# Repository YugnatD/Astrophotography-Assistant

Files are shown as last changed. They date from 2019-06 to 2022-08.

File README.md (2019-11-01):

# Astrophotography-Assistant

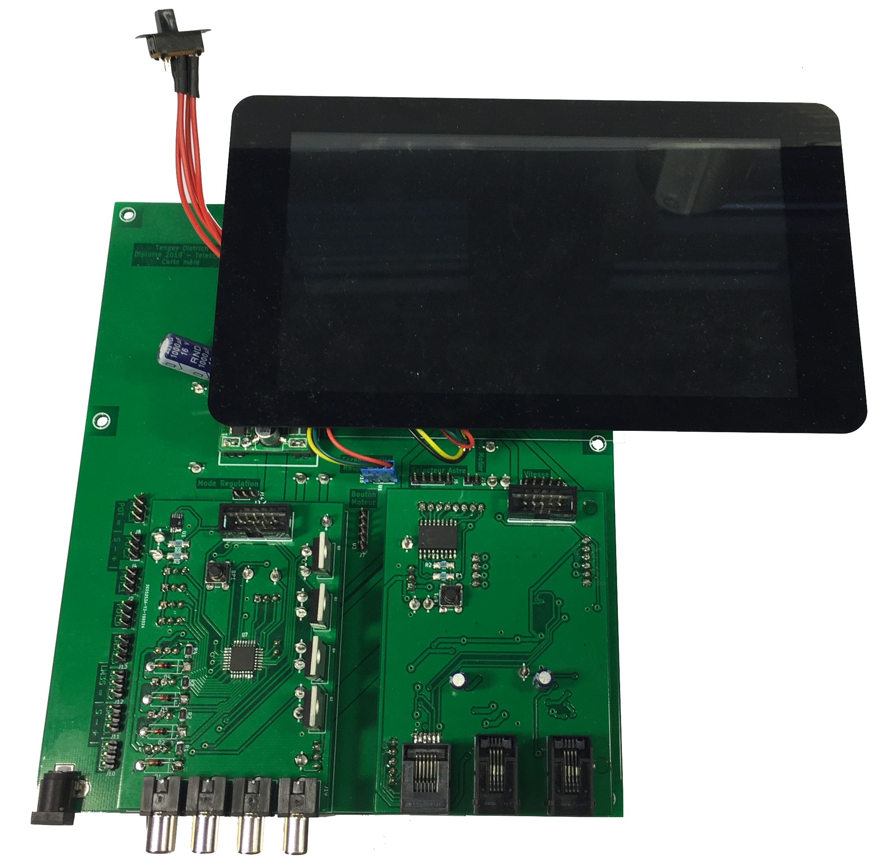
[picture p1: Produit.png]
Astrophotography-Assistant


The project has two utility :
Make an automatic regulation of the temperature of the mirror of a newtonian telescope.
Recreate a card to controle motor of a NEQ5 mount, to add more correction speed, and planetary speed.

There is a raspberry pi integrated to the card that can control a guiding camera using PHD2.

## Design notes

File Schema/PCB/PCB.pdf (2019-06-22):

9.5.Dossier de fabrication des circuits imprimés

Projet / produit : | Diplôme 2019 - Télescope

Description :

Quantités : | 1 pièce _ pièces / lot de fabrication _ pièces / an

Circuit :

Nom : | Carte Mere
Numéro : | ND (non disponible)
Révision : | 3
Date de création : | 28.05.2019 | Auteur : | Tanguy Dietrich

Historique des modifications :

Rév. | Date | Auteur | Détails des modifications
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
Spécification du PCB :

Nature du matériel isolant : | Bakélite | FR-2 | ___
Epoxy | FR-4 | ___
Autre : ___
Epaisseur du PCB : | 0.5 mm | 0.8 mm | | 1.0 mm | 1.2 mm
| 1.6 mm | 2.0 mm | | autre : _ mm
Nombre de couches : | Simple face
Double face
Multicouches, nombre de couches = X

Epaisseur des couches cuivre :
Externe | 18 P | 35 P | 75 P | 105 P | autre :
_
Interne | 18 P | 35 P | 75 P | 105 P | autre :
_
Largeur minimum des pistes : | 0.508 | mm / | 20m | inch
Largeur minimum entre pistes : | 0.254 | mm / | 10m | inch

Liste des documents :

Liste du matériel | Page 3
Dimensions du PCB | Page 4
Plan de perçage | Page 5
Plan | d’implantation
dessous
| Page 6
Plan | d’implantation
dessus
| Page 6
Print : vue de dessous | Page 7
Print : vue de dessus | Page 7
Points tests | Page 8
Fichier Gerber | ___

Liste du matériel :

Références | Composant | N° article Distrelec | Quantité | Pu [CHF] | Ptot [CHF]
C1 | 100uF 16V radial 5mm | 300-92-017 | 1 | 0.063 | 0.063
J1 | Connecteur jack-DC | 301-29-715 | 1 | 0.4335 | 0.4335
J2; J4; J8; J9; J10; J11; J12; J13; J14 | Connecteur 3 pin Male | 300-93-644 | 9 | 0.1317 | 1.1853
J3 | Connecteur 2*20 Femelle (raspberry Pi) | 300-93-679 | 1 | 2.05 | 2.05
J5; J6; J7 | Connecteur 5 pins Male | 300-93-646 | 3 | 0.2346 | 0.7038
J15 | Connecteur 2 pins Male | 300-93-652 | 1 | 0.176 | 0.176
J16; J17; J19; J20; J21; J22; J23; J24; J25 | Cosse poignard | | 9
J18 | Connecteur 4 pins Male | 300-93-645 | 1 | 0.1761 | 0.1671
JP1 | Connecteur 3 Pin male modifier | 300-93-644 | 2 | 0.1317 | 0.2634
R1; R2; R3; R4; R5; R6; R7; R8; R9; R10; R11; R12; R13 | Résistance SMD 1206 10 [kOhm] | 300-56-987 | 13 | 0.0285 | 0.3705
U1 | Carte moteur | | 1 | 18.1567 | 18.1567
J3 | Raspberry Pi 3 B+ | 301-09-158 | 1 | 39.6 | 39.6
J3 | LCD 7 pouces pour Raspberry Pi | 300-37-316 | 1 | 86.90 | 86.90
U2 | Carte LM2576 | | 1 | 4.6161 | 4.6161
U3 | Carte Température | | 1 | 55.44 | 55.44
U3,U2 | Connecteur 2 pins femelles | 300-93-662 | 5 | 0.5385 | 2.6925
U3,U1 | Connecteur 3 pins femelles | 300-93-663 | 11 | 0.8973 | 9.8703
U1 | Connecteur 4 pins femelles | 300-93-664 | 1 | 0.8973 | 0.8973
U1 | Connecteur 5 pins femelles | 300-93-665 | 1 | 0.9972 | 0.9972
U1 | Connecteur 6 pins femelles | 300-93-666 | 1 | 0.9971 | 0.9971
U1 | Connecteur 8 pins femelles | 300-93-668 | 1 | 1.14 | 1.14
PCB carte Mere | | | 1 | 2.98 | 2.98
Prix total = | | | | 229.6998 [CHF]

Dimensions de la carte :

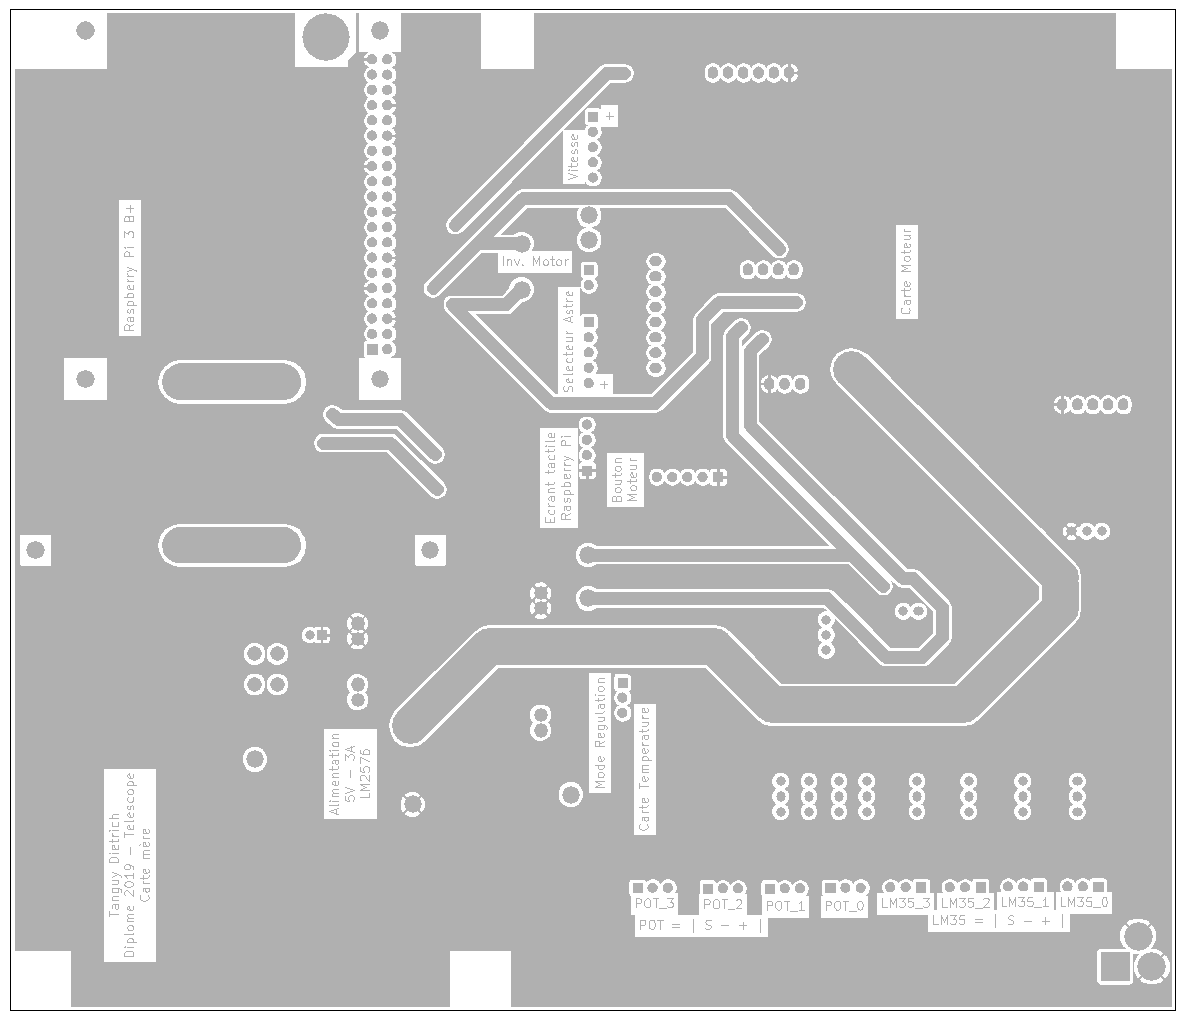
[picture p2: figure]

194mm x 166.7mm

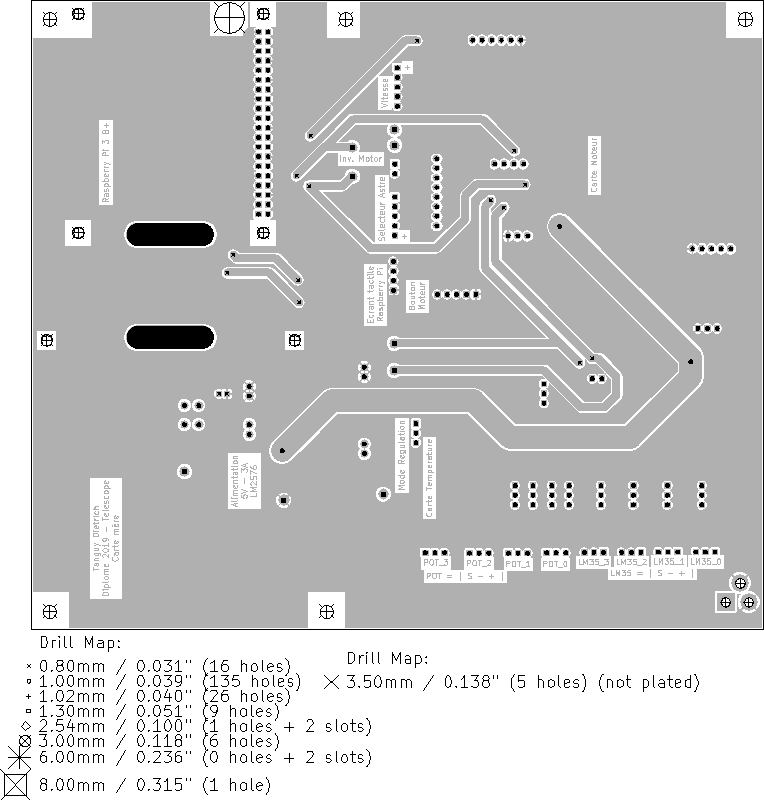
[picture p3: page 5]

Plan de perçage :

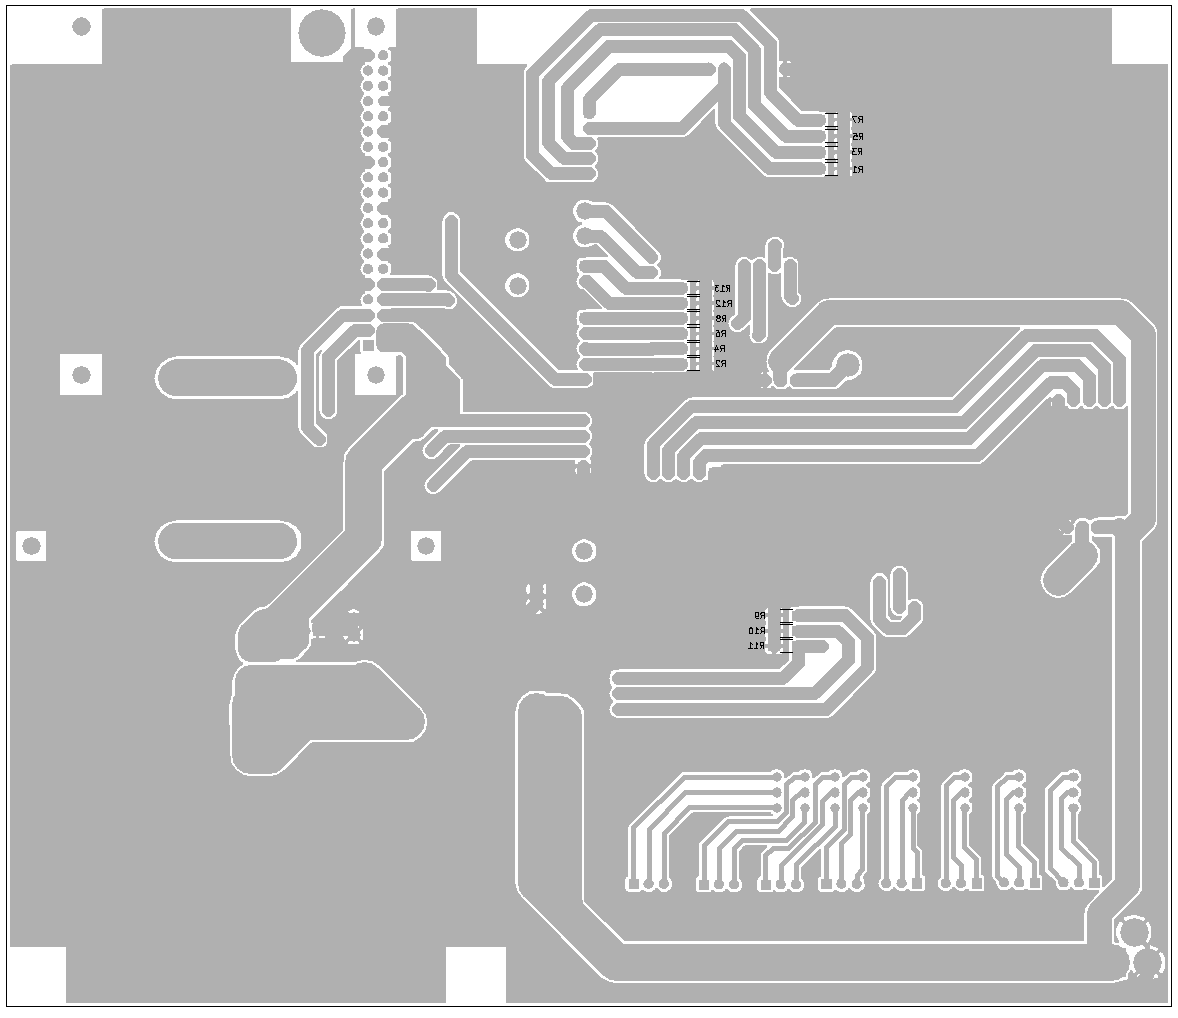
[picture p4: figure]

Plan d’implantation dessous :

Plan d’implantation dessus :

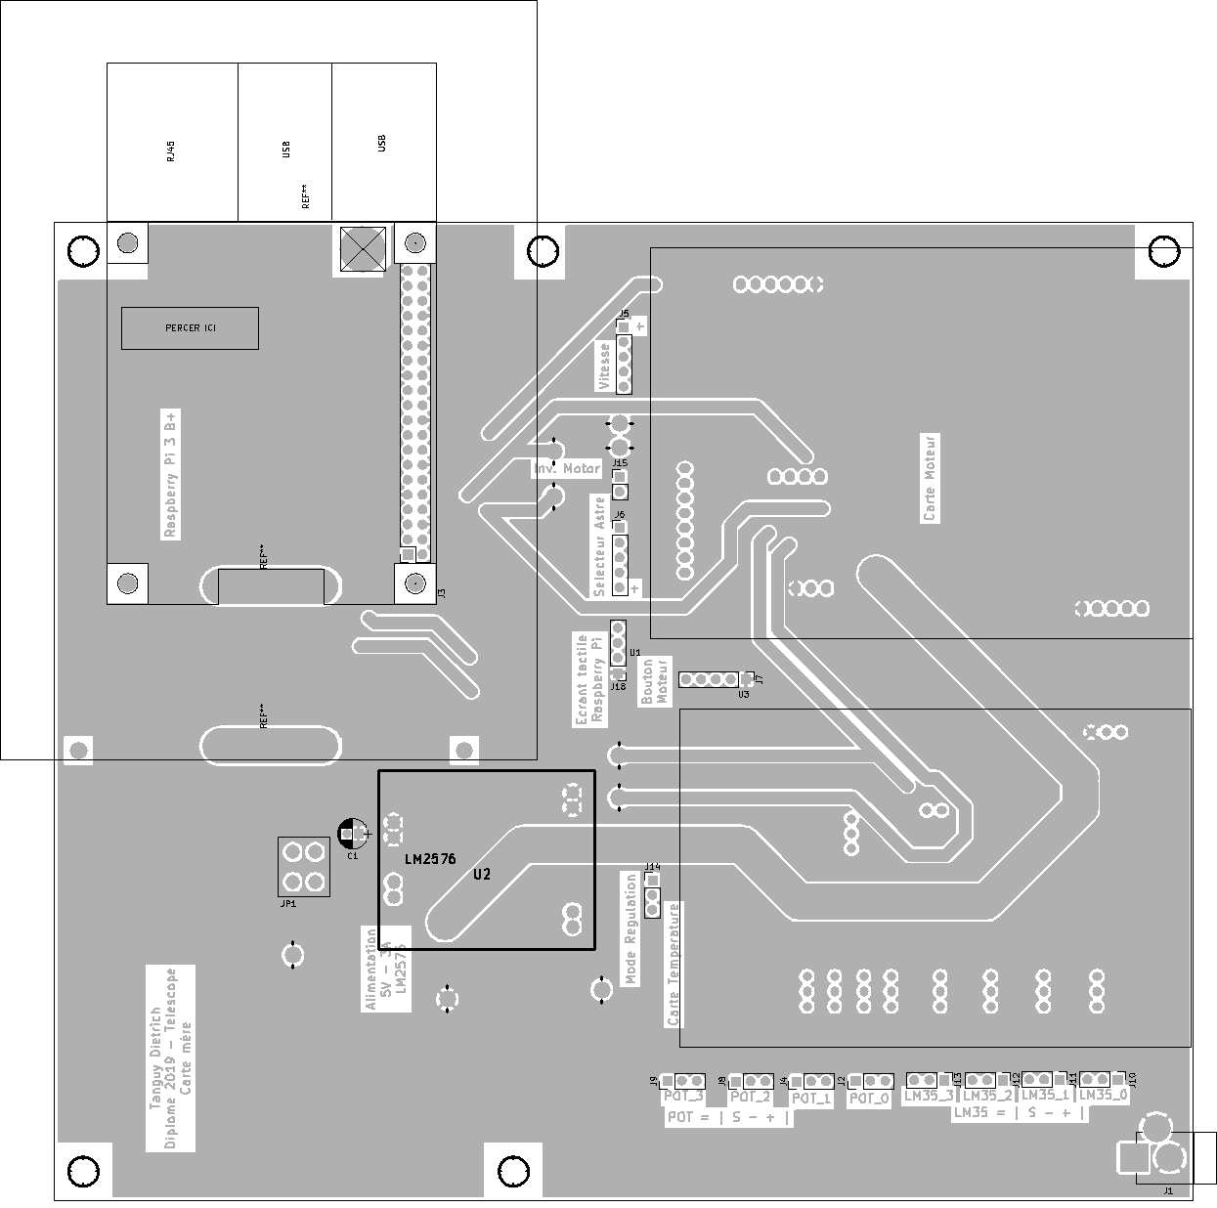
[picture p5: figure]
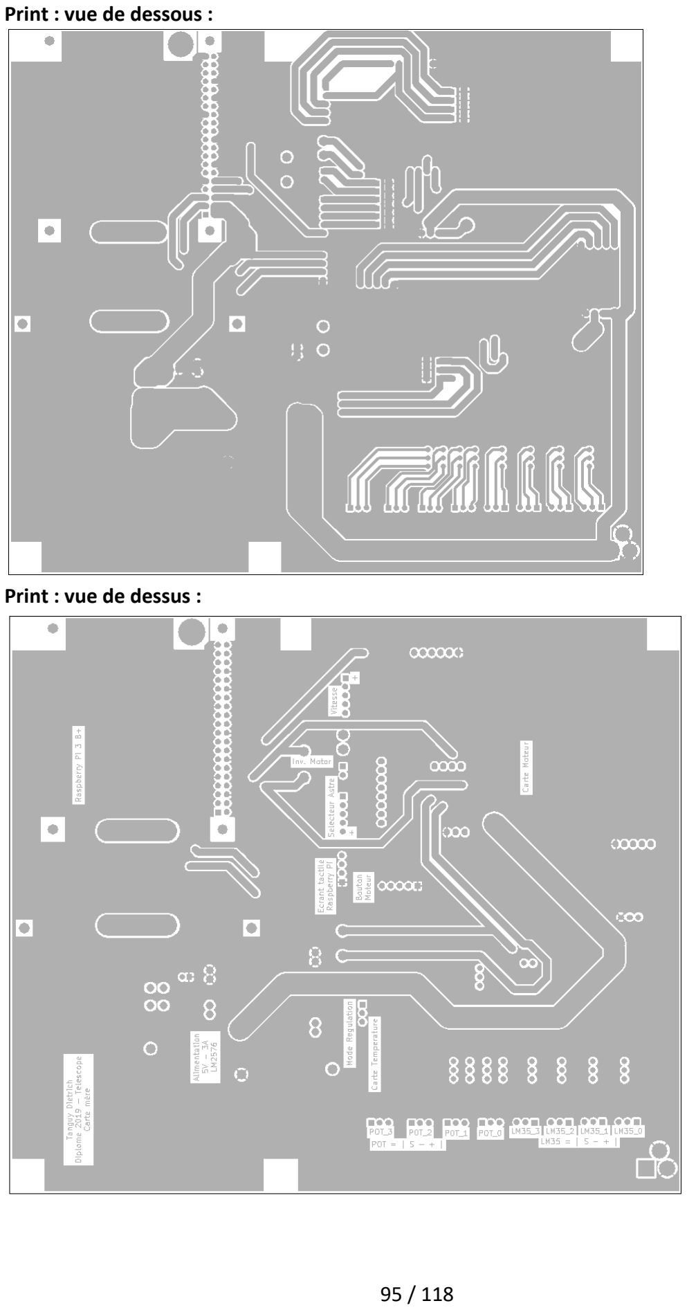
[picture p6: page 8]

Print : vue de dessous :

Print : vue de dessus :

Points tests :

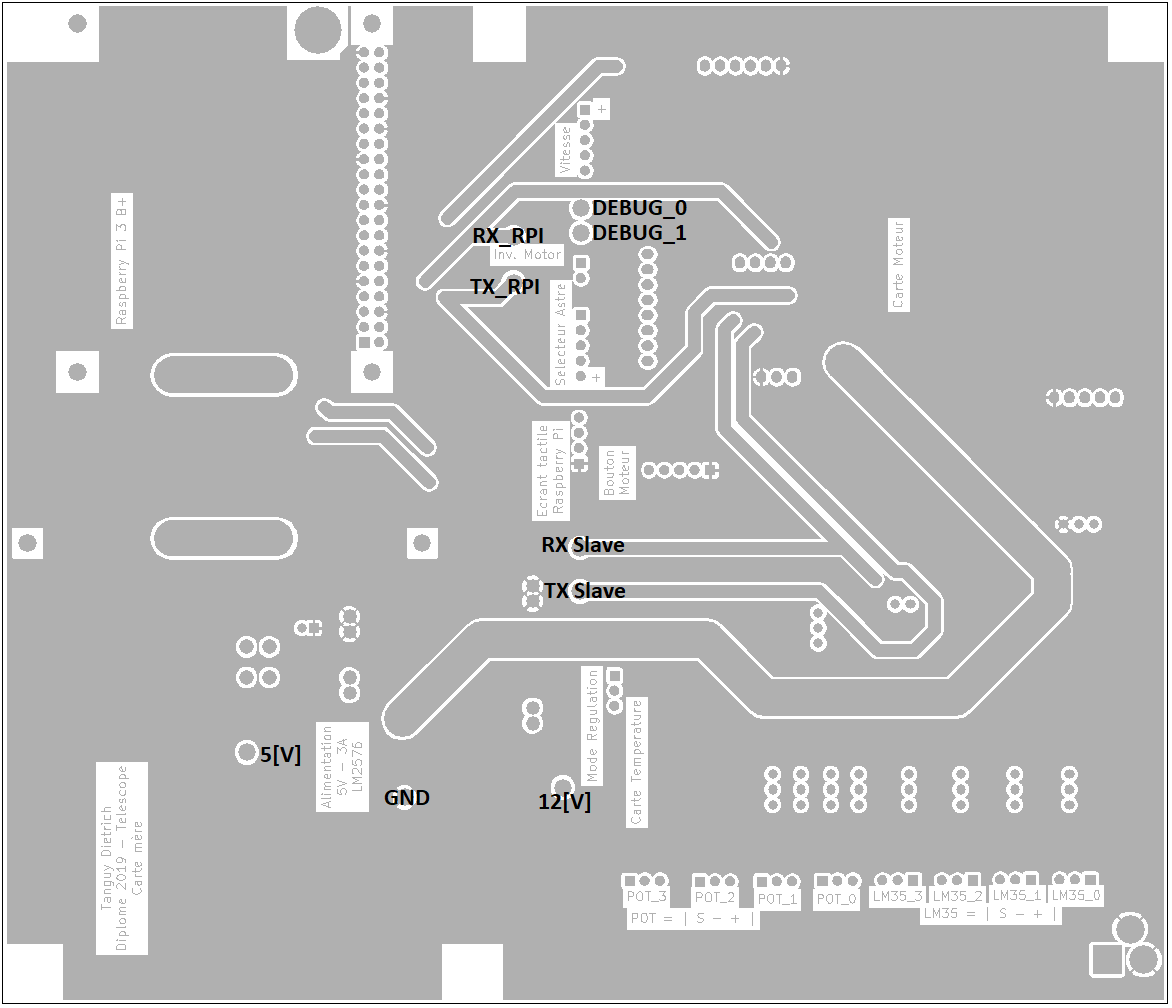
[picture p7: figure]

Projet / produit : | Diplôme 2019 - Télescope

Description :

Quantités : | 1 pièce _ pièces / lot de fabrication _ pièces / an

Circuit :

Nom : | Carte de gestion de la température
Numéro : | ND (Non disponible)
Révision : | 0
Date de création : | 17.09.2018 | Auteur : | Tanguy Dietrich

Historique des modifications :

Rév. | Date | Auteur | Détails des modifications
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
Spécification du PCB :

Nature du matériel isolant : | Bakélite | FR-2 | ___
Epoxy | FR-4 | ___
Autre : ___
Epaisseur du PCB : | 0.5 mm | 0.8 mm | | 1.0 mm | 1.2 mm
| 1.6 mm | 2.0 mm | | autre : _ mm
Nombre de couches : | Simple face
Double face
Multicouches, nombre de couches = X

Epaisseur des couches cuivre :
Externe | 18 P | 35 P | 75 P | 105 P | autre :
_
Interne | 18 P | 35 P | 75 P | 105 P | autre :
_
Largeur minimum des pistes : | 0.508 | mm / | 20m | inch
Largeur minimum entre pistes : | 0.254 | mm / | 10m | inch

Liste des documents :

Liste du matériel | Page 3
Dimensions du PCB | Page 4
Plan de perçage | Page 5
Plan | d’implantation
dessous
| Page 6
Plan | d’implantation
dessus
| Page 6
Print : vue de dessous | Page 7
Print : vue de dessus | Page 7
Points tests | Page 8
Fichier Gerber | ___

Liste du matériel :

Références | Composant | Référence fabricant | Quantité | Pu [CHF] | Ptot [CHF]
BP1 | Bouton Poussoir | 301-18-595 | 1 | 0.2111 | 0.2111
C1 | 100nF SMD 1206 | 300-67-988 | 1 | 0.1094 | 0.1094
C11 | 1uF SMD 1206 | 300-86-875 | 1 | 0.0496 | 0.0496
D1,D2,D3,D4 | 1N4148 | 300-92-887 | 4 | 0.0175 | 0.07
J1; J2; J3; J4; J5; J6; J7; J8; J9; J13 | Connecteur 3 pins male | 300-93-644 | 10 | 0.1317 | 1.317
J12 | Connecteur 10 pins | 300-12-021 | 1 | 0.87 | 0.87
J18; J19; J24; J25 | Connecteur RCJ | 490-RCJ-041 | 4 | 1.36 | 5.44
Q1; Q2; Q3; Q4 | IRL3705 TO-220 | 171-18-037 | 4 | 1.91 | 7.64
R1; R2; R3; R4, | Résistance 18k 1206 | 300-56-931 | 4 | 0.0344 | 0.1376
R5; R6 ;R15 ;R16 ;R17 | Résistance 1k 1206 | 300-56-986 | 5 | 0.0285 | 0.1425
U1 | EEH210 | 300-73-044 | 1 | 10.30 | 10.30
U7 | C8051F38C | | 1 | 1.44 | 1.44
PCB | PCB carte température | | 1 | 1 | 1
LM35 | LM35 capteur température | 173-26-716 | 4 | 3.2 | 12.8
potentiomètre | | 164-35-367 | 4 | 3.65 | 14.6
Prix total = | | | | 55.4432 [CHF]

Dimensions de la carte :

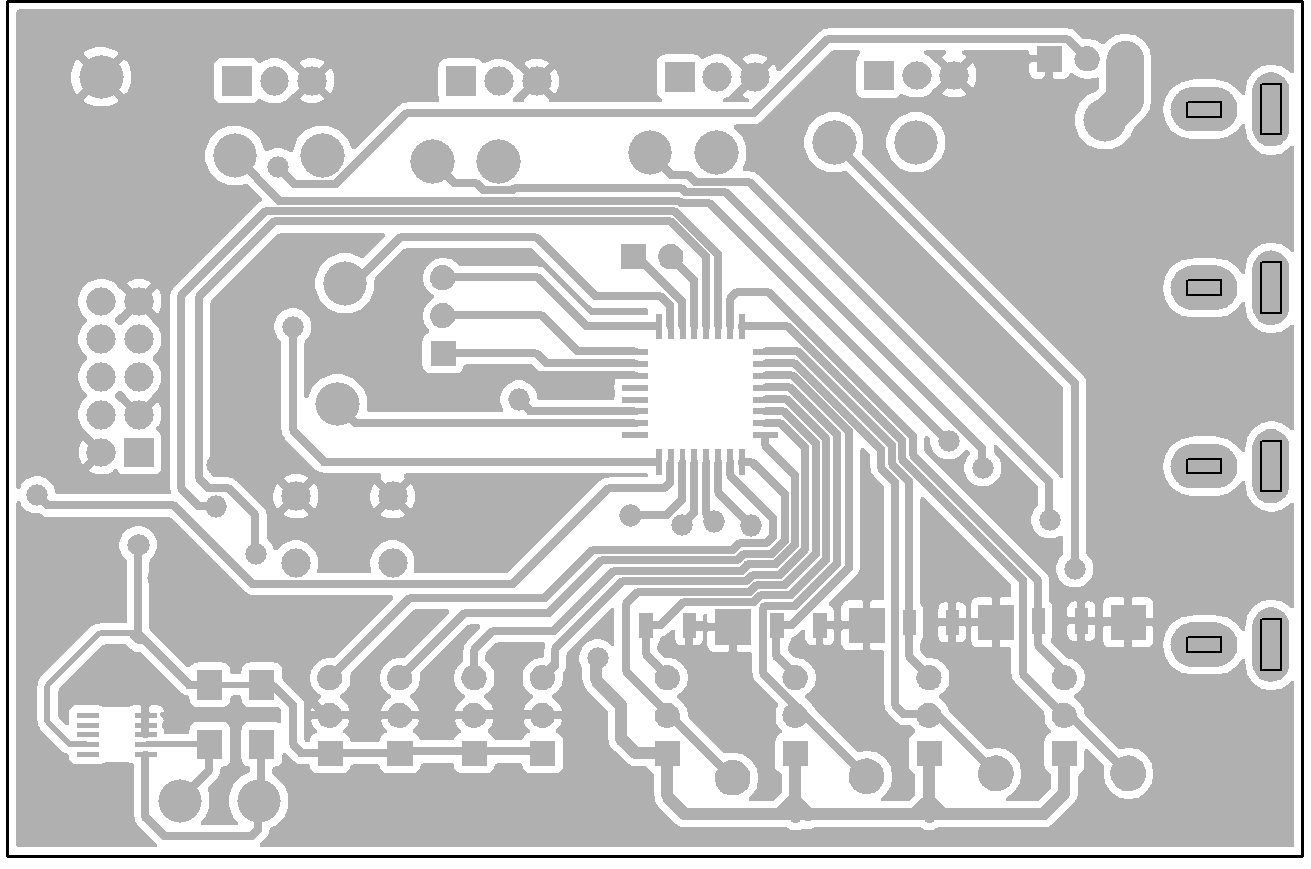
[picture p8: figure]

La carte fait 87.1mm x 57.5 mm

Plan de perçage :

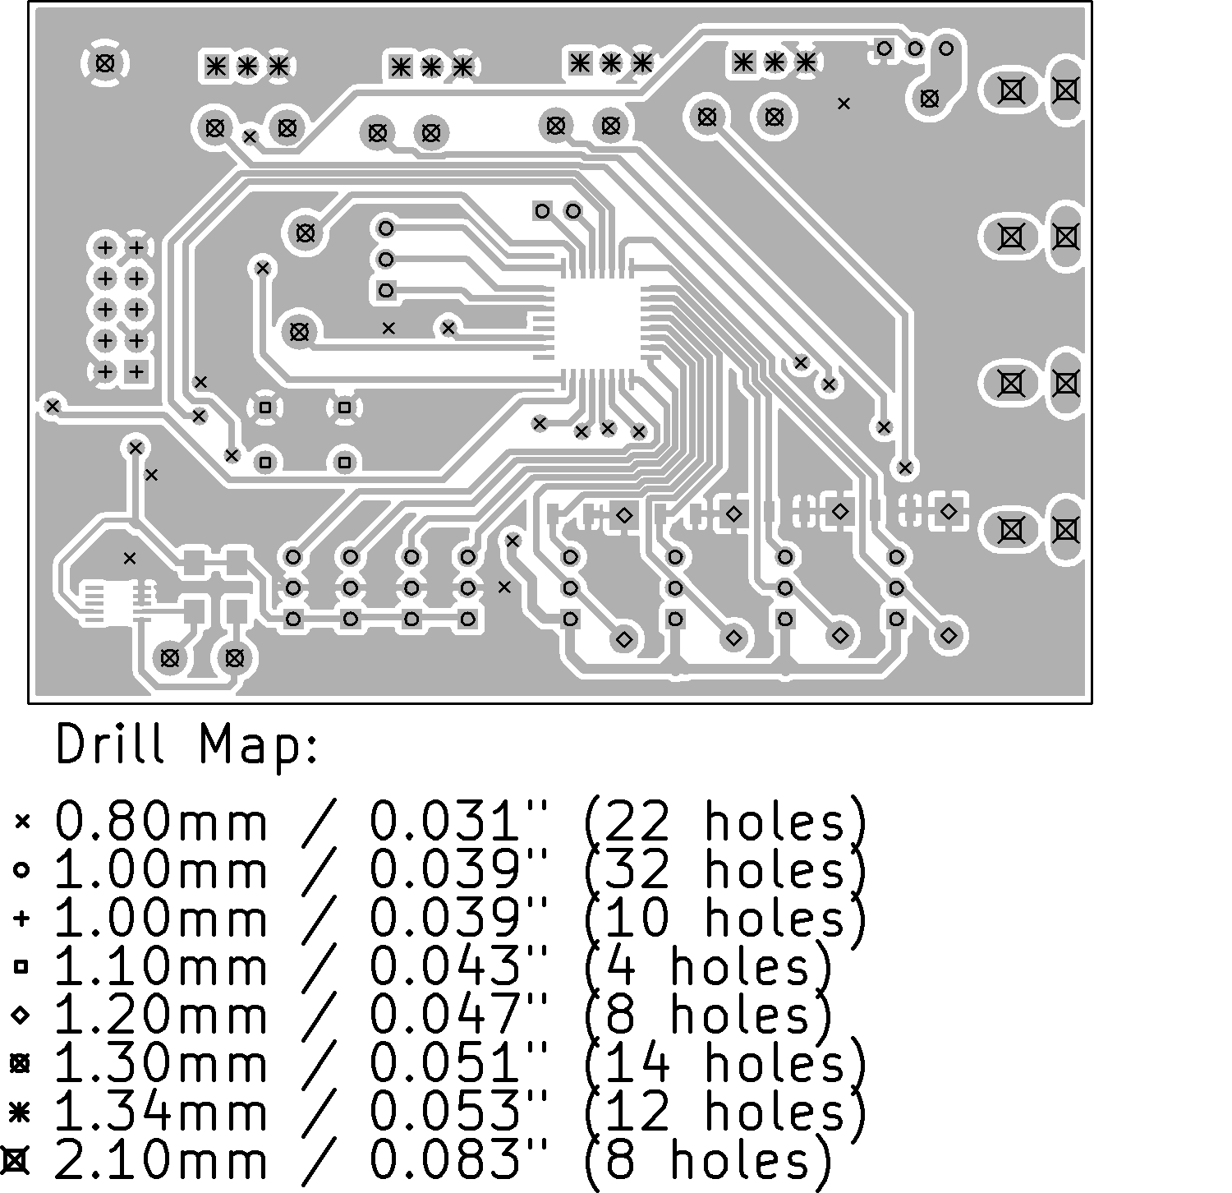
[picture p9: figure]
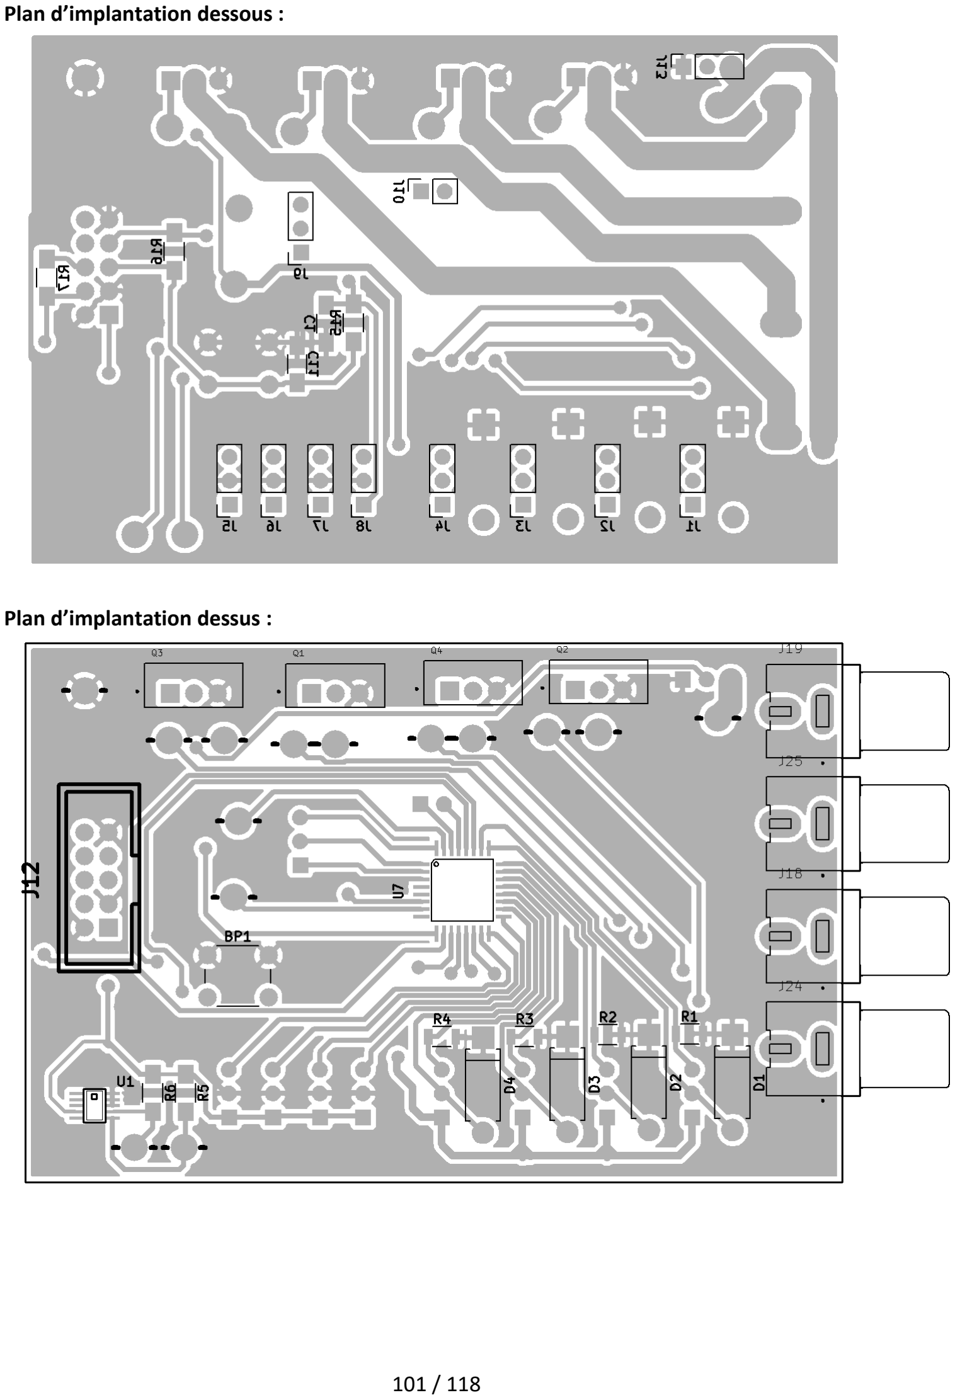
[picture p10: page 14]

Plan d’implantation dessous :

Plan d’implantation dessus :

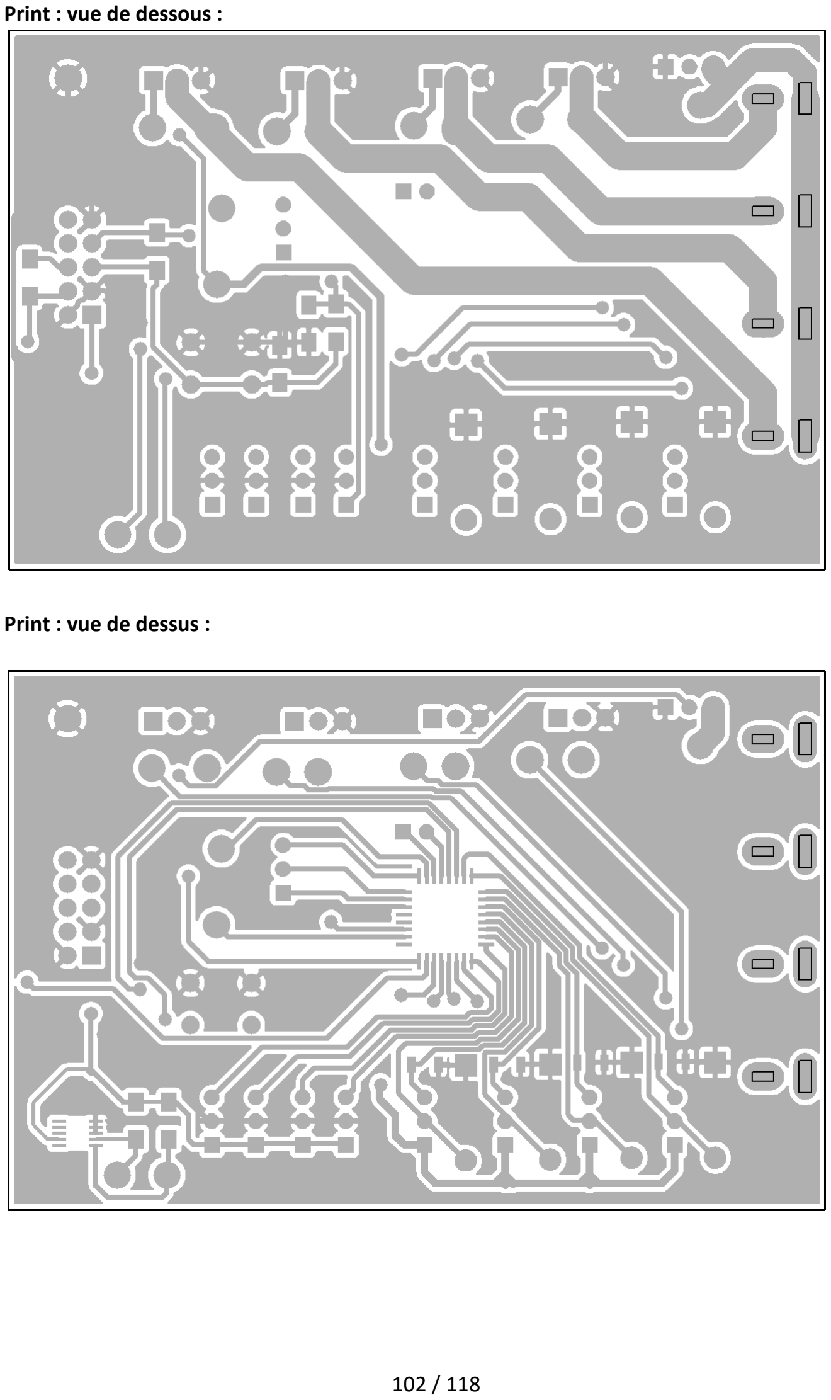
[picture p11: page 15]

Print : vue de dessous :

Print : vue de dessus :

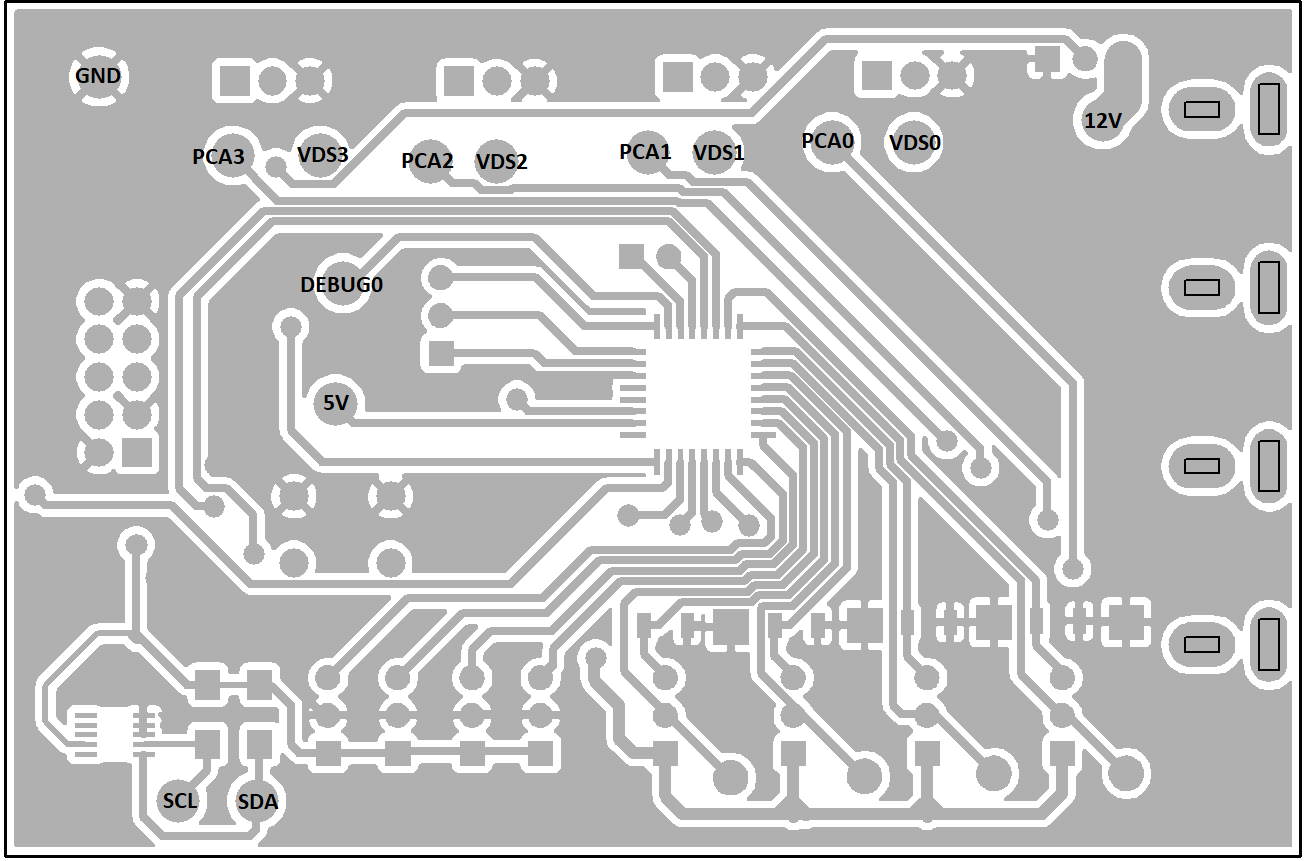
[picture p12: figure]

Points tests :

Projet / produit : | Diplôme 2019 - Télescope

Description :

Quantités : | 1 pièce _ pièces / lot de fabrication _ pièces / an

Circuit :

Nom : | Alimentation 5V – 3A
Numéro : | ND (non disponible)
Révision : | 0
Date de création : | 17.09.2018 | Auteur : | Tanguy Dietrich

Historique des modifications :

Rév. | Date | Auteur | Détails des modifications
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
Spécification du PCB :

Nature du matériel isolant : | Bakélite | FR-2 | ___
Epoxy | FR-4 | ___
Autre : ___
Epaisseur du PCB : | 0.5 mm | 0.8 mm | | 1.0 mm | 1.2 mm
| 1.6 mm | 2.0 mm | | autre : _ mm
Nombre de couches : | Simple face
Double face
Multicouches, nombre de couches = X

Epaisseur des couches cuivre :
Externe | 18 P | 35 P | 75 P | 105 P | autre :
_
Interne | 18 P | 35 P | 75 P | 105 P | autre :
_
Largeur minimum des pistes : | 0.508 | mm / | 20m | inch
Largeur minimum entre pistes : | 0.254 | mm / | 10m | inch

Liste des documents :

Schéma électrique | Page 3
Liste du matériel | Page 3
Dimensions du PCB | Page 4
Plan de perçage | Page 5
Plan | d’implantation
dessous
| Page 6
Plan | d’implantation
dessus
| Page 6
Print : vue de dessous | Page 7
Print : vue de dessus | Page 7
Points tests | Page 8
Fichier Gerber | ___

Schéma électrique :

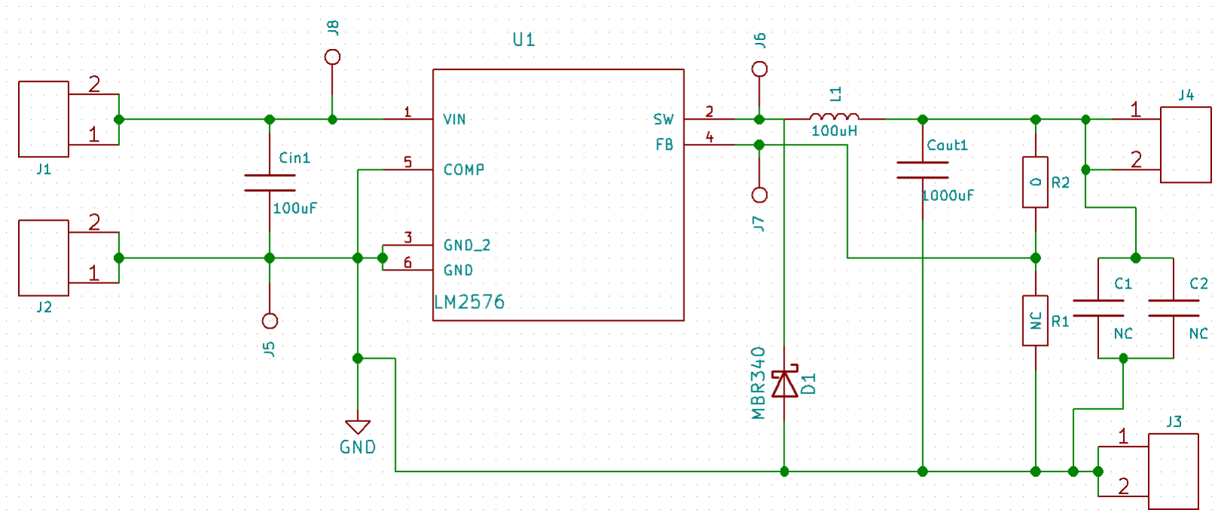
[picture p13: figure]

Liste du matériel :

Références | Composant | Référence fabricant | Quantité | Pu [CHF] | Ptot [CHF]
J1…J4 | Connecteur 2 poles | 300-93-652 | 4 | 0.176 | 0.704
Cin1 | Condensateur 100uF SMD | 167-31-200 | 1 | 0.2172 | 0.2172
Cout1 | Condensateur 1000uF | 300-92-035 | 1 | 0.2415 | 0.2415
J5…J8 | Cosse | | 4
U1 | LM2576 | 300-19-258 | 1 | 2.35 | 2.35
D1 | MBR340 | 170-09-528 | 1 | 0.4106 | 0.4106
L1 | 100uH SMD | 301-28-799 | 1 | 0.6928 | 0.6928
Prix total = | | | | 4.6161 [CHF]

Dimensions de la carte :

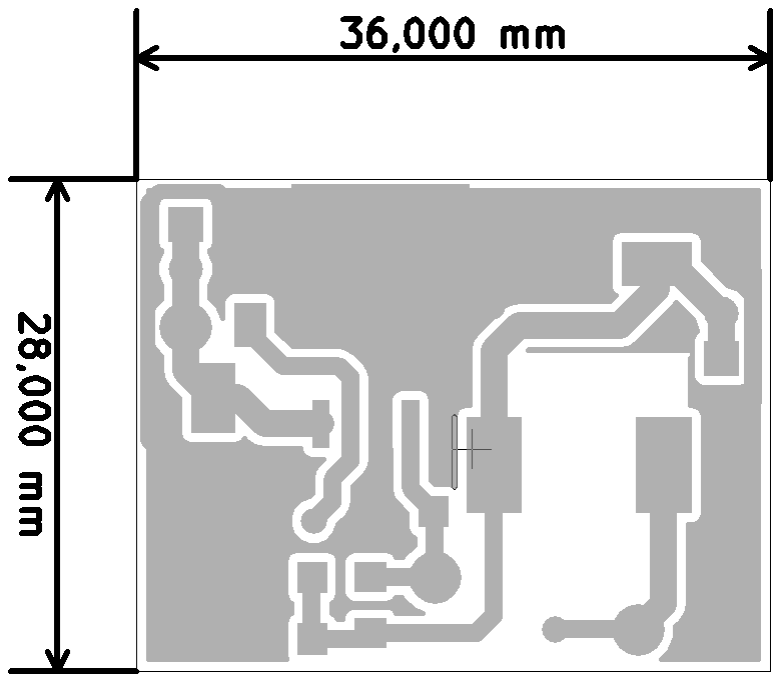
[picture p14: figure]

Plan de perçage :

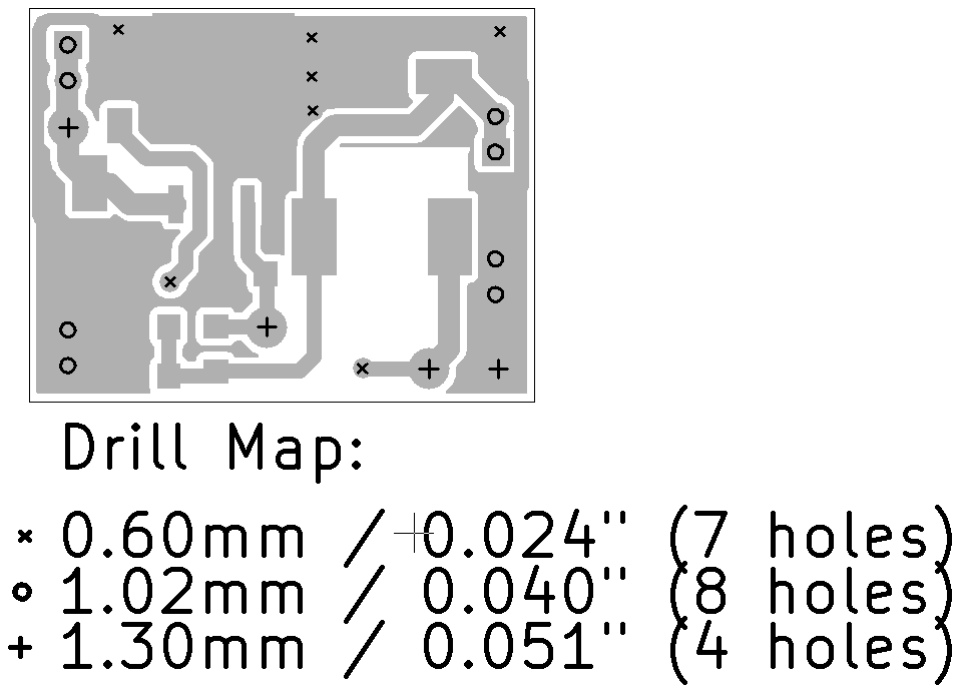
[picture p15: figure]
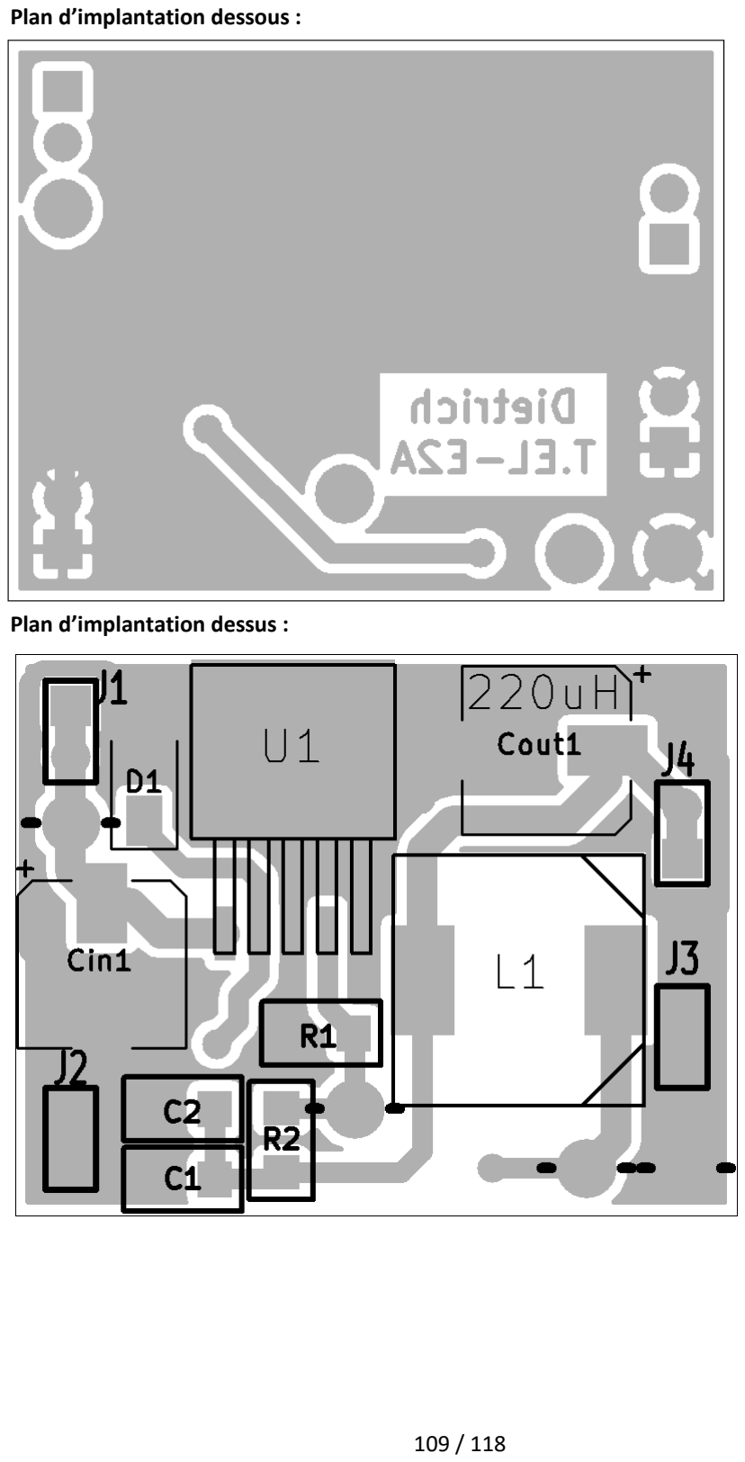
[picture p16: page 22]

Plan d’implantation dessous :

Plan d’implantation dessus :

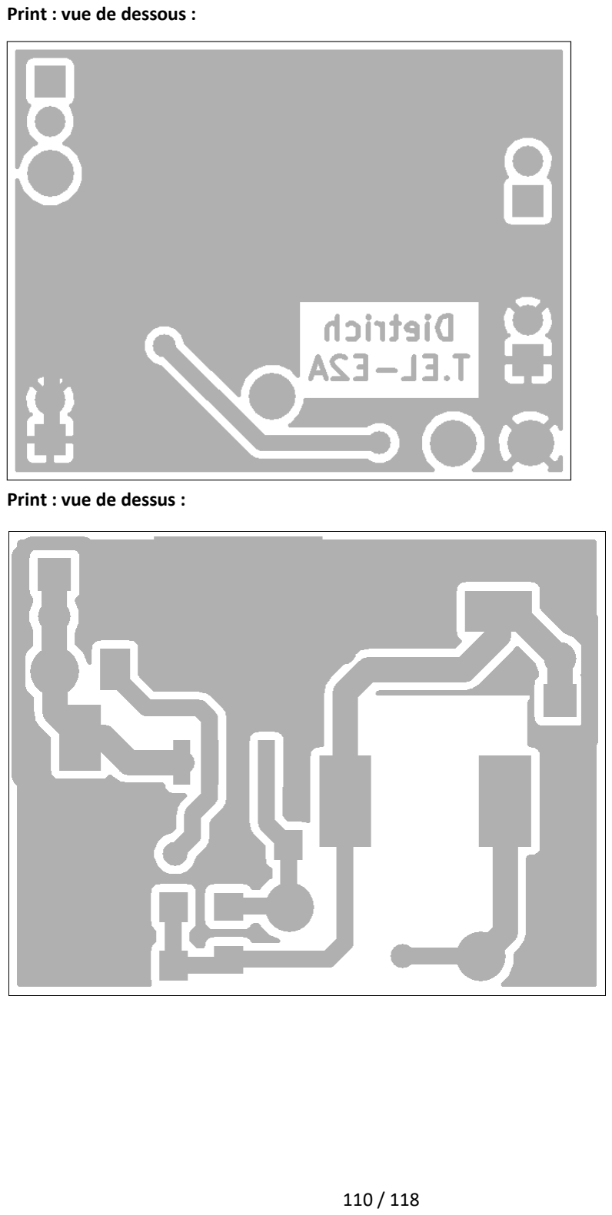
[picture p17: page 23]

Print : vue de dessous :

Print : vue de dessus :

Points tests :

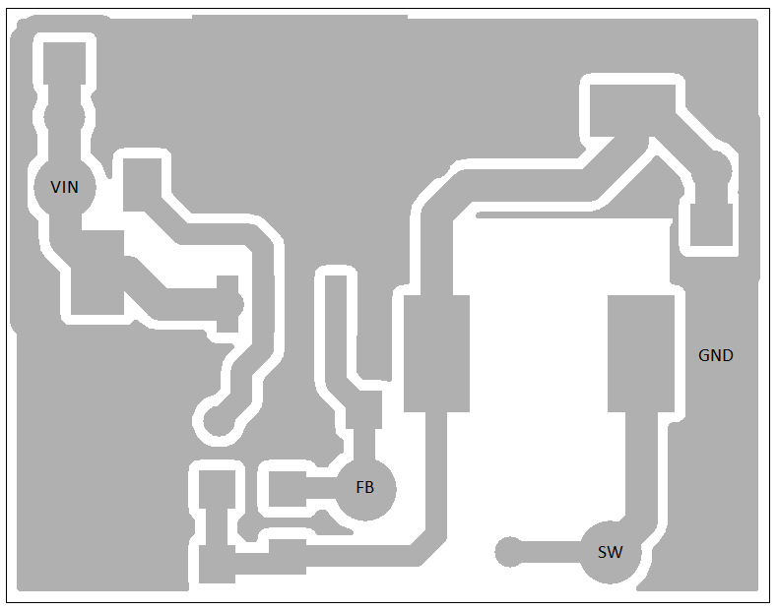
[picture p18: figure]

Projet / produit : | Diplôme 2019 - Télescope

Description :

Quantités : | 1 pièce _ pièces / lot de fabrication _ pièces / an

Circuit :

Nom : | Carte de gestion des moteur
Numéro : | ND (Non disponible)
Révision : | 0
Date de création : | 17.09.2018 | Auteur : | Tanguy Dietrich

Historique des modifications :

Rév. | Date | Auteur | Détails des modifications
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
Spécification du PCB :

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

Liste des documents :

Schéma électrique | Page 3
Liste du matériel | Page 3
Dimensions du PCB | Page 4
Plan de perçage | Page 5
Plan | d’implantation
dessous
| Page 6
Plan | d’implantation
dessus
| Page 6
Print : vue de dessous | Page 7
Print : vue de dessus | Page 7
Points tests | Page 8
Fichier Gerber | ___

Liste du matériel :

Références | Composant | Référence fabricant | Quantité | Pu [CHF] | Ptot [CHF]
BP1 | Bouton Poussoir 6mm | 301-18-595 | 1 | 0.2111 | 0.2111
C1; C2 | 0.47uF 1206 | 300-86-945 | 2 | 0.052 | 0.104
C3; C4; C5; C6; C7; C12 | 0.1uF 1206 | 300-67-988 | 6 | 0.1094 | 0.6564
C8; C13 | 100uF radial 5mm | 300-92-017 | 2 | 0.063 | 0.126
C9; C10 | 0.01uF 1206 | 300-66-368 | 2 | 0.144 | 0.288
C11 | 1uF 1206 | 300-86-875 | 1 | 0.0496 | 0.0496
J1 | Barrette 8 pin male | 300-93-649 | 1 | 0.4189 | 0.4189
J2 | Barrette 4 pin male | 300-93-645 | 1 | 0.1761 | 0.1761
J3 | Connecteur RJ12 | Mouser :538-95501-6669 | 1 | 0.776 | 0.776
J4 | Barrette 6 pin male | 300-93-647 | 1 | 0.2991 | 0.2991
J5 | Barrette 3 pin male | 300-93-644 | 1 | 0.1317 | 0.1317
J12 | Connecteur 10 pin | 300-12-021 | 1 | 0.87 | 0.87
J13; J14; J15; J16 | Cosse | | 4
J17; J18 | RJ11 | Mouser : 538-95009-7441 | 2 | 0.797 | 1.594
J19 | Barrette 5 pin male | 300-93-646 | 1 | 0.2346 | 0.2346
R1; R2; R9; R10 | Résistance 10k SMD 1206 | 300-56-987 | 4 | 0.0285 | 0.114
R3; R4; R5; R6 ;R15 ;R16 ;R17 | Résistance 1k SMD 1206 | 300-56-986 | 7 | 0.0285 | 0.1995
R7; R8 | Résistance 1M SMD 1206 | 300-56-919 | 2 | 0.0305 | 0.061
R11; R12; R13; R14 | Résistance 5.6Ohm SMD 1206 | 160-18-949 | 4 | 0.1071 | 0.4284
U1 | MCP23008 | 300-46-590 | 1 | 1.09 | 1.09
U2 | CD4081 | 300-18-498 | 1 | 0.4809 | 0.4809
U3 ;U4 | DRV8825 | Mouser :595-DRV8825PWPR | 2 | 3.72 | 7.44
U7 | C8051F38C | | 1 | 1.41 | 1.41
PCB | PCB Carte température | | 1 | 1 | 1
Prix total = | | | | 18.1567 [CHF]

Dimensions de la carte :
La carte fait 92.3mm par 66.5mm

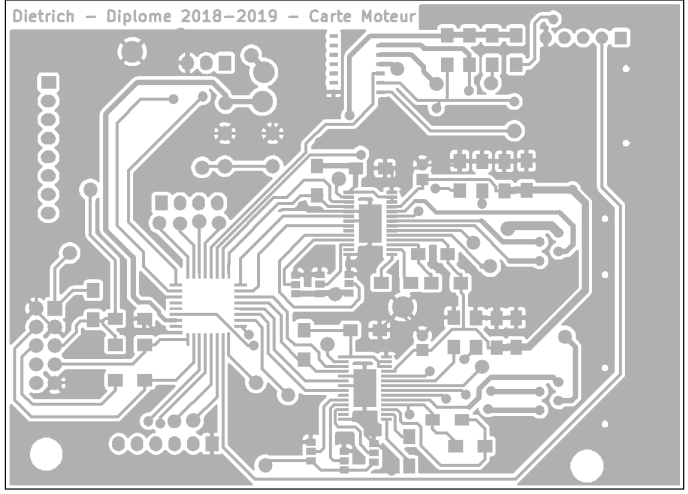
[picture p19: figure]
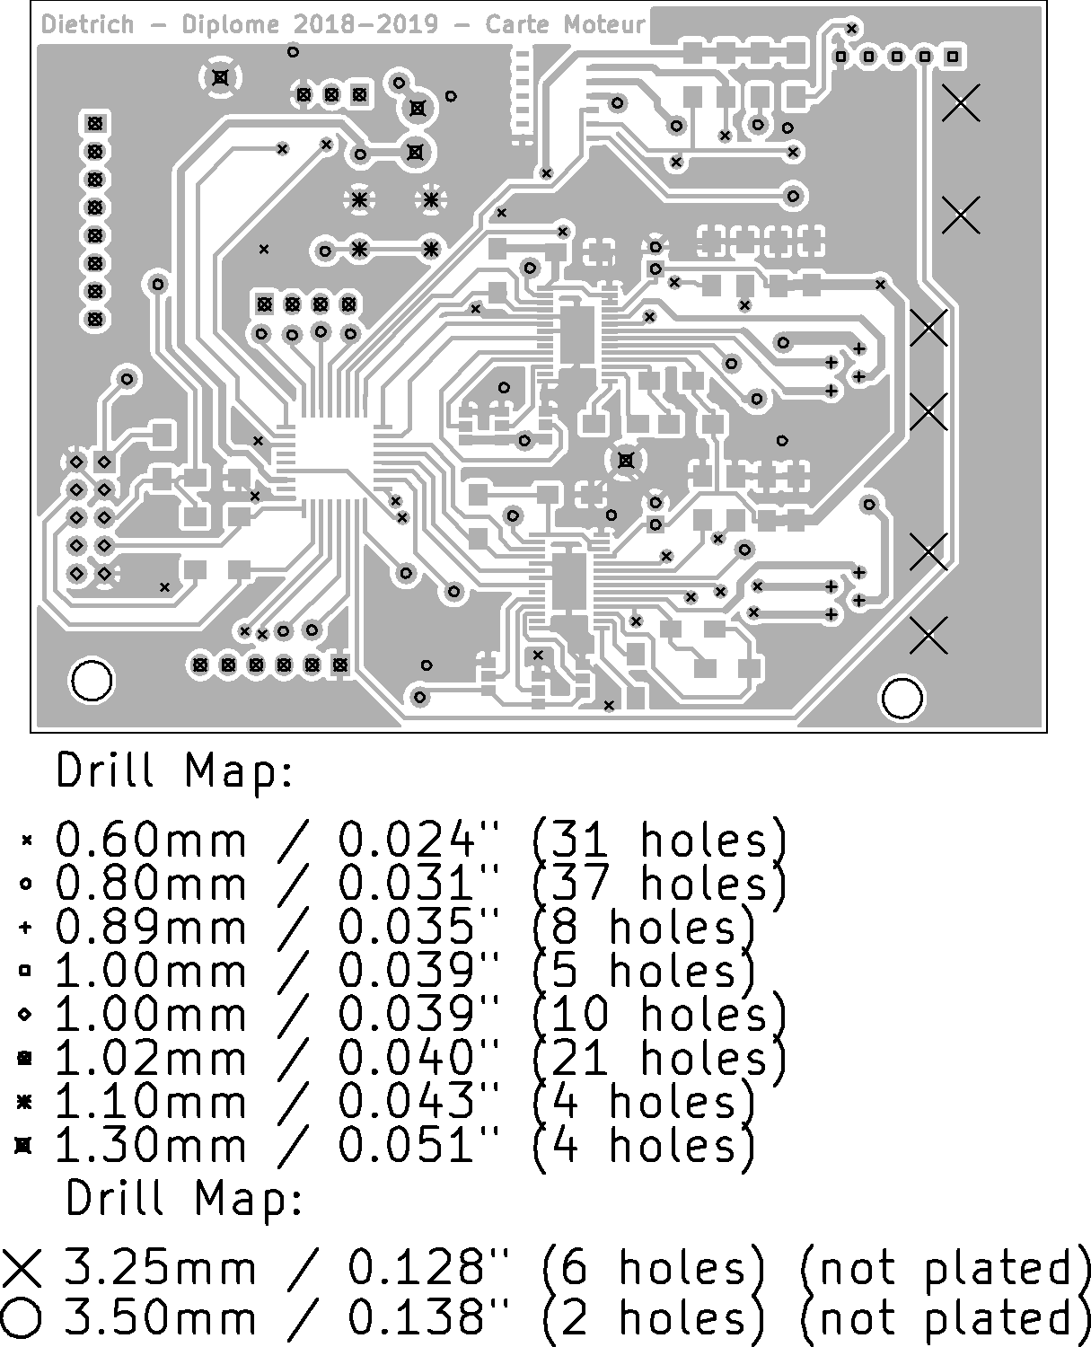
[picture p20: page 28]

Plan de perçage :

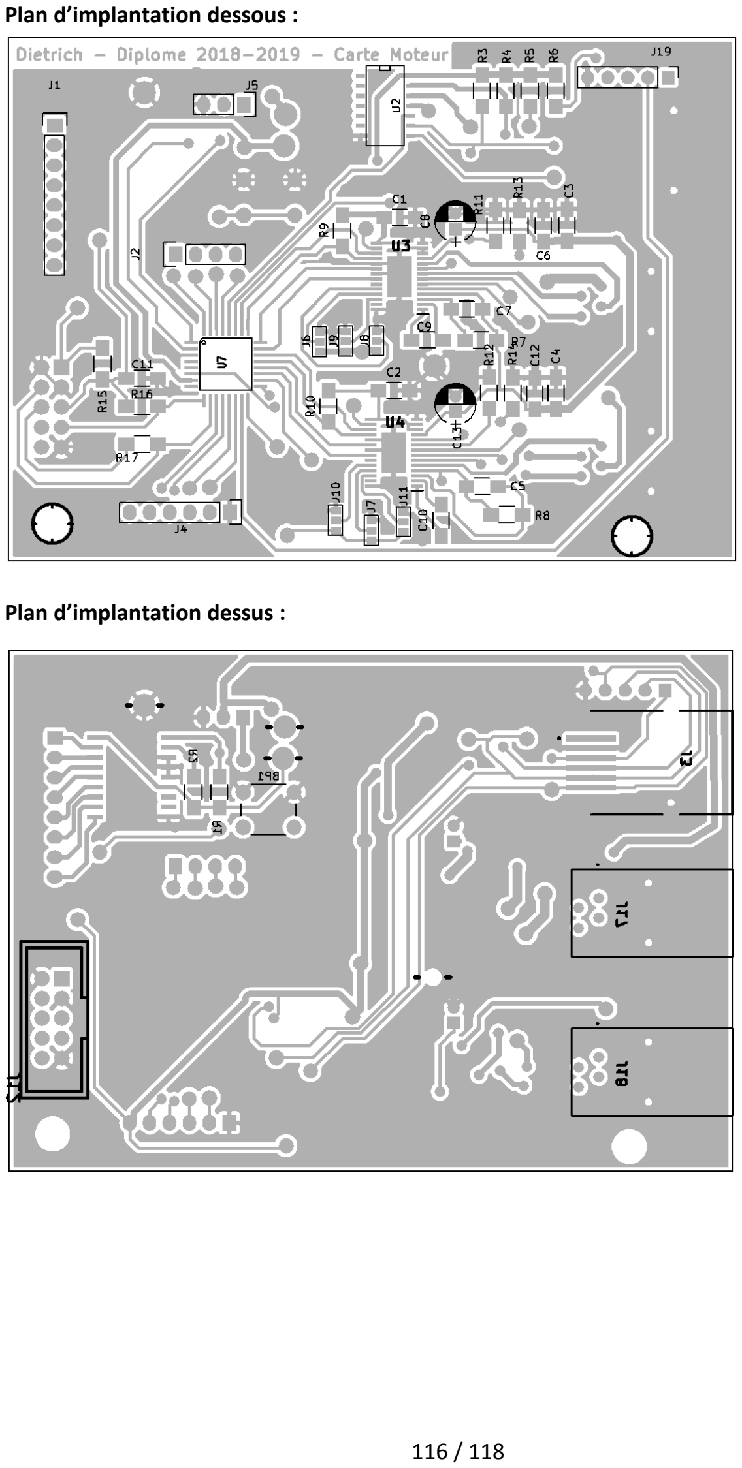
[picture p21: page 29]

Plan d’implantation dessous :

Plan d’implantation dessus :

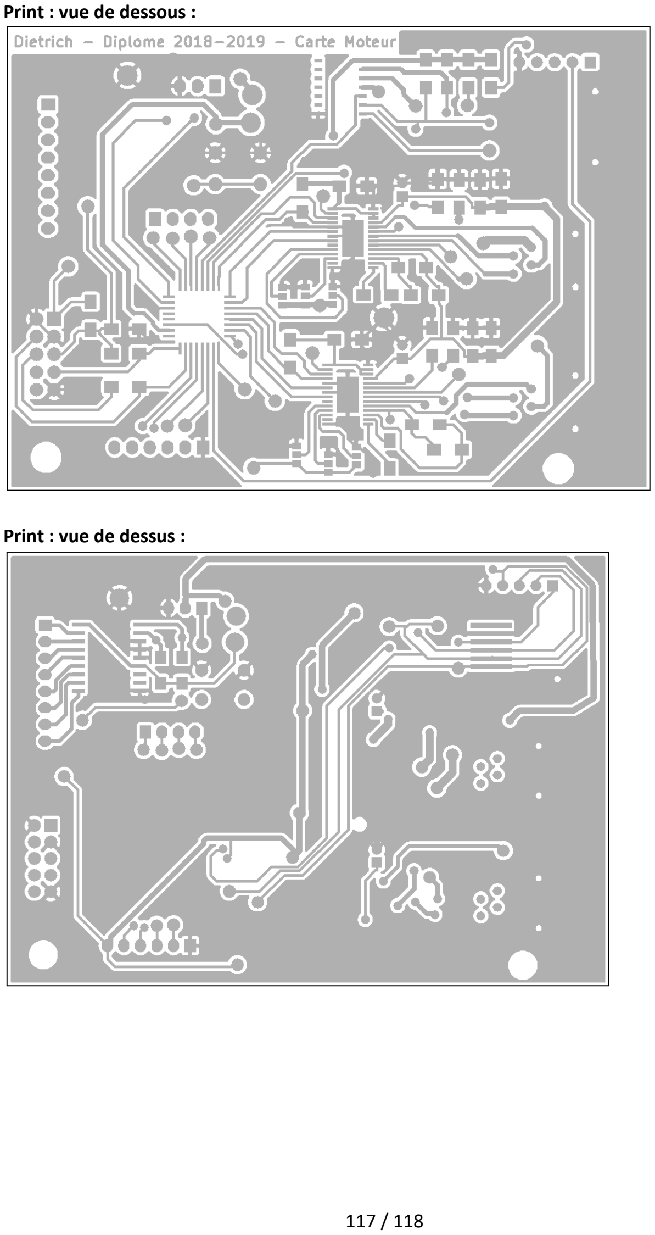
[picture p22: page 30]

Print : vue de dessous :

Print : vue de dessus :

Points tests :

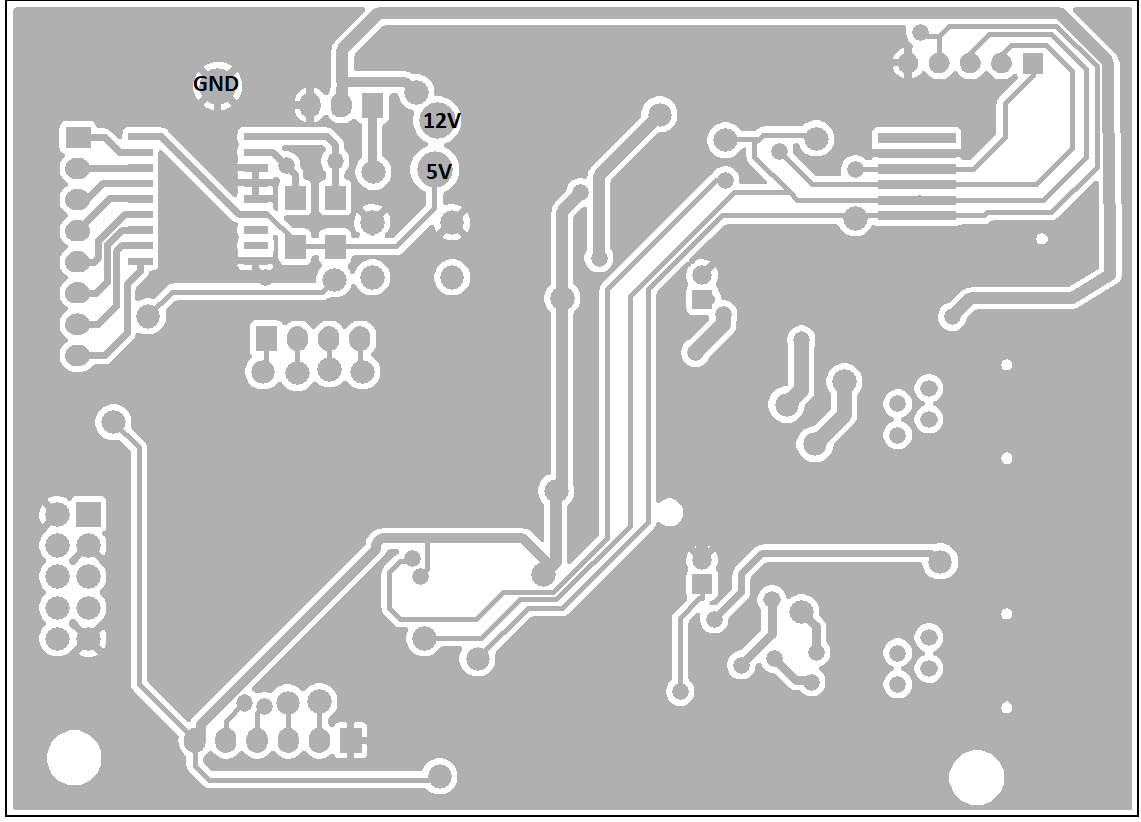
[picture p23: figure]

### 9.6. Listing des codes sources

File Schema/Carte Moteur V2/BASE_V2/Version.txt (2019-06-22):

Version

2.0 	Renommer les empreintes selon nouvelle procédure
2.1	TSC suppression de la couche top
	Redimensionnement texte 1 sur 1,5 épaisseur 0,2

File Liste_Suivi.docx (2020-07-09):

Astre | Numéro
Etoile | 0
Lune | 1
Soleil | 2
Saturne | 3
Jupiter | 4
Comète (C/2020 F3 Neowise) | 5
ISS | 6

Vitesse de correction | Numéro
x0,1 | 0
x0,2 | 1
x0,3 | 2
x0,4 | 3
x0,5 | 4
x2 | 5
X8 | 6
X16 | 7
X48 | 8

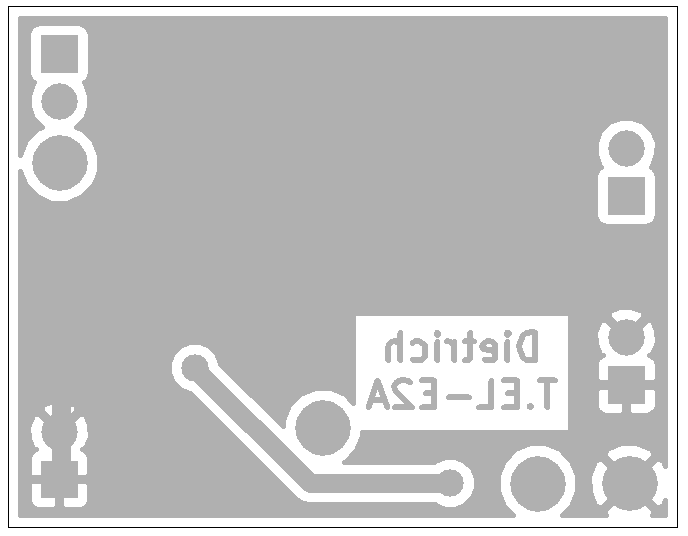
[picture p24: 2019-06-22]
Schema/Charge_active_Dietrich_V2/Image/Bottom.PNG

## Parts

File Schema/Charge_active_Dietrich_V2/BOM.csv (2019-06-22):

Source: | C:/Users/DIETRICHT_ELEC/Desktop/Diplome_Telescope_Dietrich_V17/Kicad_Telescope_V6/Charge_active_Dietrich_V2/Charge_active_Dietrich.sch
Date: | 24.05.2019 11:29
Tool: | Eeschema 4.0.7
Generator: | C:/Program Files/KiCad/bin/scripting/plugins/bom_csv_grouped_by_value.py
Component Count: | 17
Individual Components:
Item | Qty | Reference(s) | Value | LibPart | Footprint | Datasheet | Champ4 | Champ5 | Champ6 | Champ7 | Champ8 | Field4 | Field5 | Field6 | Field7 | Field8
 |  | C1 | NC | BASE_V2:C | base_V2:SM_C_1206
 |  | C2 | NC | BASE_V2:C | base_V2:SM_C_1206
 |  | Cin1 | 100uF | BASE_V2:C | Capacitors_SMD:CP_Elec_8x10
 |  | Cout1 | 1000uF | BASE_V2:C | Capacitors_SMD:CP_Elec_8x10
 |  | D1 | MBR340 | device:D_Schottky | Diodes_SMD:D_SMA
 |  | J1 | CON2 | BASE_V2:CON2 | base_V2:TSC_CON2_SIL
 |  | J2 | CON2 | BASE_V2:CON2 | base_V2:TSC_CON2_SIL
 |  | J3 | CON2 | BASE_V2:CON2 | base_V2:TSC_CON2_SIL
 |  | J4 | CON2 | BASE_V2:CON2 | base_V2:TSC_CON2_SIL
 |  | J5 | CON1 | BASE_V2:CON1 | base_V2:TSC_CON1_poignard
 |  | J6 | CON1 | BASE_V2:CON1 | base_V2:TSC_CON1_poignard
 |  | J7 | CON1 | BASE_V2:CON1 | base_V2:TSC_CON1_poignard
 |  | J8 | CON1 | BASE_V2:CON1 | base_V2:TSC_CON1_poignard
 |  | L1 | 100uH | BASE_V2:L | DR127-221-R:INDM125125X800N
 |  | R1 | NC | BASE_V2:R | base_V2:SM_R_1206
 |  | R2 | 0 | BASE_V2:R | base_V2:SM_R_1206
 |  | U1 | LM2575HVS-ADJ | LM2575HVS-ADJ:LM2575HVS-ADJ | LM2575HVS-ADJ:TO170P1435X457-6N | TO-263-5 Texas Instruments | Texas Instruments | 4.76 USD | LM2575HVS-ADJ | Warning | Conv DC-DC 4V to 60V Step Down Single-Out 1.23V to 57V 1A 6-Pin_5+Tab_ TO-263 Tube | Texas Instruments | 4.76 USD | LM2575HVS-ADJ | Warning | Conv DC-DC 4V to 60V Step Down Single-Out 1.23V to 57V 1A 6-Pin_5+Tab_ TO-263 Tube
Collated Components:
Item | Qty | Reference(s) | Value | LibPart | Footprint | Datasheet | Champ4 | Champ5 | Champ6 | Champ7 | Champ8 | Field4 | Field5 | Field6 | Field7 | Field8
1 | 2 | C1; C2 | NC | BASE_V2:C | base_V2:SM_C_1206
2 | 1 | Cin1 | 100uF | BASE_V2:C | Capacitors_SMD:CP_Elec_8x10
3 | 1 | Cout1 | 1000uF | BASE_V2:C | Capacitors_SMD:CP_Elec_8x10
4 | 1 | D1 | MBR340 | device:D_Schottky | Diodes_SMD:D_SMA
5 | 4 | J1; J2; J3; J4 | CON2 | BASE_V2:CON2 | base_V2:TSC_CON2_SIL
6 | 4 | J5; J6; J7; J8 | CON1 | BASE_V2:CON1 | base_V2:TSC_CON1_poignard
7 | 1 | L1 | 100uH | BASE_V2:L | DR127-221-R:INDM125125X800N
8 | 1 | R1 | NC | BASE_V2:R | base_V2:SM_R_1206
9 | 1 | R2 | 0 | BASE_V2:R | base_V2:SM_R_1206
10 | 1 | U1 | LM2575HVS-ADJ | LM2575HVS-ADJ:LM2575HVS-ADJ | LM2575HVS-ADJ:TO170P1435X457-6N | TO-263-5 Texas Instruments | Texas Instruments | 4.76 USD | LM2575HVS-ADJ | Warning | Conv DC-DC 4V to 60V Step Down Single-Out 1.23V to 57V 1A 6-Pin_5+Tab_ TO-263 Tube | Texas Instruments | 4.76 USD | LM2575HVS-ADJ | Warning | Conv DC-DC 4V to 60V Step Down Single-Out 1.23V to 57V 1A 6-Pin_5+Tab_ TO-263 Tube

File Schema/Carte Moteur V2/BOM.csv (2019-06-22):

Source:
Date: | 24.05.2019 10:07
Tool: | Eeschema 4.0.7
Generator:
Component Count: | 55
Individual Components:
Item | Qty | Reference(s) | Value | LibPart | Footprint | Datasheet | Description | Manufacturer_Name | Manufacturer_Part_Number | Mouser Part Number | Mouser Price/Stock
 |  | BP1 | POUSSOIR_ON | Carte_Principale-cache:POUSSOIR_ON | Buttons_Switches_THT:SW_PUSH_6mm
 |  | C1 | 0.47uF | device:C | Capacitors_SMD:C_1206_HandSoldering
 |  | C2 | 0.47uF | device:C | Capacitors_SMD:C_1206_HandSoldering
 |  | C3 | 0.1uF | device:C | Capacitors_SMD:C_1206_HandSoldering
 |  | C4 | 0.1uF | device:C | Capacitors_SMD:C_1206_HandSoldering
 |  | C5 | 0.1uF | device:C | Capacitors_SMD:C_1206_HandSoldering
 |  | C6 | 0.1uF | device:C | Capacitors_SMD:C_1206_HandSoldering
 |  | C7 | 0.1uF | device:C | Capacitors_SMD:C_1206_HandSoldering
 |  | C8 | 100uF | device:C | Carte_Principale:CP_Radial_D5.0mm_P2.00mm
 |  | C9 | 0.01uF | device:C | Capacitors_SMD:C_1206_HandSoldering
 |  | C10 | 0.01uF | device:C | Capacitors_SMD:C_1206_HandSoldering
 |  | C11 | 1uF | device:C | Capacitors_SMD:C_1206_HandSoldering
 |  | C12 | 0.1uF | device:C | Capacitors_SMD:C_1206_HandSoldering
 |  | C13 | 100uF | device:C | Carte_Principale:CP_Radial_D5.0mm_P2.00mm
 |  | J1 | Conn_01x08 | conn:Conn_01x08 | Pin_Headers:Pin_Header_Straight_1x08
 |  | J2 | Conn_01x04 | conn:Conn_01x04 | Pin_Headers:Pin_Header_Straight_1x04
 |  | J3 | RJ12 | conn:RJ12 | Carte_Principale:RJ12
 |  | J4 | Conn_01x06 | conn:Conn_01x06 | Pin_Headers:Pin_Header_Straight_1x06
 |  | J5 | Conn_01x03 | conn:Conn_01x03 | Pin_Headers:Pin_Header_Straight_1x03
 |  | J6 | GS3 | conn:GS3 | Connectors:GS3
 |  | J7 | GS3 | conn:GS3 | Connectors:GS3
 |  | J8 | GS3 | conn:GS3 | Connectors:GS3
 |  | J9 | GS3 | conn:GS3 | Connectors:GS3
 |  | J10 | GS3 | conn:GS3 | Connectors:GS3
 |  | J11 | GS3 | conn:GS3 | Connectors:GS3
 |  | J12 | HEADER_10P | Carte_Principale:HEADER_10P | Carte_Principale:JTAG
 |  | J13 | COSSE | Carte_Principale-cache:COSSE | base_V2:TSC_CON1_poignard
 |  | J14 | COSSE | Carte_Principale-cache:COSSE | base_V2:TSC_CON1_poignard
 |  | J15 | COSSE | Carte_Principale-cache:COSSE | base_V2:TSC_CON1_poignard
 |  | J16 | COSSE | Carte_Principale-cache:COSSE | base_V2:TSC_CON1_poignard
 |  | J17 | 95009-7441 | Carte_Principale-cache:95009-7441 | Carte_Principale:RJ11-95009-7441 | https://componentsearchengine.com/Datasheets/1/95009-7441.pdf | RJ11 R/A PCB modular jack; w/panel stops Molex 4P4C Right Angle PCB Mount RJ11 Modular Jack Connector 95009 | Molex | 95009-7441 | 538-95009-7441 | https://www.mouser.com/Search/Refine.aspx?Keyword=538-95009-7441
 |  | J18 | 95009-7441 | Carte_Principale-cache:95009-7441 | Carte_Principale:RJ11-95009-7441 | https://componentsearchengine.com/Datasheets/1/95009-7441.pdf | RJ11 R/A PCB modular jack; w/panel stops Molex 4P4C Right Angle PCB Mount RJ11 Modular Jack Connector 95009 | Molex | 95009-7441 | 538-95009-7441 | https://www.mouser.com/Search/Refine.aspx?Keyword=538-95009-7441
 |  | J19 | CONN_01X05 | Carte_Principale-cache:CONN_01X05 | Pin_Headers:Pin_Header_Straight_1x05_Pitch2.54mm
 |  | R1 | 10k | device:R | Resistors_SMD:R_1206_HandSoldering
 |  | R2 | 10k | device:R | Resistors_SMD:R_1206_HandSoldering
 |  | R3 | 1k | device:R | Resistors_SMD:R_1206_HandSoldering
 |  | R4 | 1k | device:R | Resistors_SMD:R_1206_HandSoldering
 |  | R5 | 1k | device:R | Resistors_SMD:R_1206_HandSoldering
 |  | R6 | 1k | device:R | Resistors_SMD:R_1206_HandSoldering
 |  | R7 | 1M | device:R | Resistors_SMD:R_1206_HandSoldering
 |  | R8 | 1M | device:R | Resistors_SMD:R_1206_HandSoldering
 |  | R9 | 10k | device:R | Resistors_SMD:R_1206_HandSoldering
 |  | R10 | 10k | device:R | Resistors_SMD:R_1206_HandSoldering
 |  | R11 | 02.févr | device:R | Resistors_SMD:R_1206_HandSoldering
 |  | R12 | 02.févr | device:R | Resistors_SMD:R_1206_HandSoldering
 |  | R13 | 02.févr | device:R | Resistors_SMD:R_1206_HandSoldering
 |  | R14 | 02.févr | device:R | Resistors_SMD:R_1206_HandSoldering
 |  | R15 | 1K | device:R | Resistors_SMD:R_1206_HandSoldering
 |  | R16 | 1K | device:R | Resistors_SMD:R_1206_HandSoldering
 |  | R17 | 1K | device:R | Resistors_SMD:R_1206_HandSoldering
 |  | U1 | MCP23008 | microchip:MCP23008 | Carte_Principale:SOIC-18
 |  | U2 | 4081 | cmos4000:4081 | base_V2:SM_SO-14
 |  | U3 | DRV8825 | Carte_Principale:DRV8825 | Carte_Principale:DRV8825
 |  | U4 | DRV8825 | Carte_Principale:DRV8825 | Carte_Principale:DRV8825
 |  | U7 | C8051F38C | Carte_Principale:C8051F38C | Carte_Principale:C8051F38C
Collated Components:
Item | Qty | Reference(s) | Value | Empreinte | Footprint | Datasheet | Description | Manufacturer_Name | Manufacturer_Part_Number | Mouser Part Number | Mouser Price/Stock
1 | 1 | BP1 | POUSSOIR_ON | Buttons_Switches_THT:SW_PUSH_6mm | Buttons_Switches_THT:SW_PUSH_6mm
2 | 2 | C1; C2 | 0.47uF | SMD 1206 | Capacitors_SMD:C_1206_HandSoldering
3 | 6 | C3; C4; C5; C6; C7; C12 | 0.1uF | SMD 1207 | Capacitors_SMD:C_1206_HandSoldering
4 | 2 | C8; C13 | 100uF | SMD 1208 | Carte_Principale:CP_Radial_D5.0mm_P2.00mm
5 | 2 | C9; C10 | 0.01uF | SMD 1209 | Capacitors_SMD:C_1206_HandSoldering
6 | 1 | C11 | 1uF | SMD 1210 | Capacitors_SMD:C_1206_HandSoldering
7 | 1 | J1 | Conn_01x08 | conn:Conn_01x08 | Pin_Headers:Pin_Header_Straight_1x08
8 | 1 | J2 | Conn_01x04 | conn:Conn_01x04 | Pin_Headers:Pin_Header_Straight_1x04
9 | 1 | J3 | RJ12 | conn:RJ12 | Carte_Principale:RJ12
10 | 1 | J4 | Conn_01x06 | conn:Conn_01x06 | Pin_Headers:Pin_Header_Straight_1x06
11 | 1 | J5 | Conn_01x03 | conn:Conn_01x03 | Pin_Headers:Pin_Header_Straight_1x03
 | 1 | J12 | HEADER_10P | Carte_Principale:HEADER_10P | Carte_Principale:JTAG
 | 4 | J13; J14; J15; J16 | COSSE | Carte_Principale-cache:COSSE | base_V2:TSC_CON1_poignard
 | 2 | J17; J18 | 95009-7441 | Carte_Principale-cache:95009-7441 | Carte_Principale:RJ11-95009-7441 | https://componentsearchengine.com/Datasheets/1/95009-7441.pdf | RJ11 R/A PCB modular jack; w/panel stops Molex 4P4C Right Angle PCB Mount RJ11 Modular Jack Connector 95009 | Molex | 95009-7441 | 538-95009-7441 | https://www.mouser.com/Search/Refine.aspx?Keyword=538-95009-7441
 | 1 | J19 | CONN_01X05 | Carte_Principale-cache:CONN_01X05 | Pin_Headers:Pin_Header_Straight_1x05_Pitch2.54mm
 | 4 | R1; R2; R9; R10 | 10k | device:R | Resistors_SMD:R_1206_HandSoldering
 | 4 | R3; R4; R5; R6 | 1k | device:R | Resistors_SMD:R_1206_HandSoldering
 | 2 | R7; R8 | 1M | device:R | Resistors_SMD:R_1206_HandSoldering
 | 4 | R11; R12; R13; R14 | 02.févr | device:R | Resistors_SMD:R_1206_HandSoldering
 | 3 | R15; R16; R17 | 1K | device:R | Resistors_SMD:R_1206_HandSoldering
 | 1 | U1 | MCP23008 | microchip:MCP23008 | Carte_Principale:SOIC-18
 | 1 | U2 | 4081 | cmos4000:4081 | base_V2:SM_SO-14
 | 2 | U3; U4 | DRV8825 | Carte_Principale:DRV8825 | Carte_Principale:DRV8825
 | 1 | U7 | C8051F38C | Carte_Principale:C8051F38C | Carte_Principale:C8051F38C

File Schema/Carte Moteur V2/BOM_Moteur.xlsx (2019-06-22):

Source:
Date: | 2019-05-24 10:07
Tool: | Eeschema 4.0.7
Generator:
Component Count: | 55
Individual Components:
Item | Qty | Reference(s) | Value | LibPart | Footprint | Datasheet | Description | Manufacturer_Name | Manufacturer_Part_Number | Mouser Part Number | Mouser Price/Stock
 |  | BP1 | POUSSOIR_ON | Carte_Principale-cache:POUSSOIR_ON | Buttons_Switches_THT:SW_PUSH_6mm
 |  | C1 | 0.47uF | device:C | Capacitors_SMD:C_1206_HandSoldering
 |  | C2 | 0.47uF | device:C | Capacitors_SMD:C_1206_HandSoldering
 |  | C3 | 0.1uF | device:C | Capacitors_SMD:C_1206_HandSoldering
 |  | C4 | 0.1uF | device:C | Capacitors_SMD:C_1206_HandSoldering
 |  | C5 | 0.1uF | device:C | Capacitors_SMD:C_1206_HandSoldering
 |  | C6 | 0.1uF | device:C | Capacitors_SMD:C_1206_HandSoldering
 |  | C7 | 0.1uF | device:C | Capacitors_SMD:C_1206_HandSoldering
 |  | C8 | 100uF | device:C | Carte_Principale:CP_Radial_D5.0mm_P2.00mm
 |  | C9 | 0.01uF | device:C | Capacitors_SMD:C_1206_HandSoldering
 |  | C10 | 0.01uF | device:C | Capacitors_SMD:C_1206_HandSoldering
 |  | C11 | 1uF | device:C | Capacitors_SMD:C_1206_HandSoldering
 |  | C12 | 0.1uF | device:C | Capacitors_SMD:C_1206_HandSoldering
 |  | C13 | 100uF | device:C | Carte_Principale:CP_Radial_D5.0mm_P2.00mm
 |  | J1 | Conn_01x08 | conn:Conn_01x08 | Pin_Headers:Pin_Header_Straight_1x08
 |  | J2 | Conn_01x04 | conn:Conn_01x04 | Pin_Headers:Pin_Header_Straight_1x04
 |  | J3 | RJ12 | conn:RJ12 | Carte_Principale:RJ12
 |  | J4 | Conn_01x06 | conn:Conn_01x06 | Pin_Headers:Pin_Header_Straight_1x06
 |  | J5 | Conn_01x03 | conn:Conn_01x03 | Pin_Headers:Pin_Header_Straight_1x03
 |  | J6 | GS3 | conn:GS3 | Connectors:GS3
 |  | J7 | GS3 | conn:GS3 | Connectors:GS3
 |  | J8 | GS3 | conn:GS3 | Connectors:GS3
 |  | J9 | GS3 | conn:GS3 | Connectors:GS3
 |  | J10 | GS3 | conn:GS3 | Connectors:GS3
 |  | J11 | GS3 | conn:GS3 | Connectors:GS3
 |  | J12 | HEADER_10P | Carte_Principale:HEADER_10P | Carte_Principale:JTAG
 |  | J13 | COSSE | Carte_Principale-cache:COSSE | base_V2:TSC_CON1_poignard
 |  | J14 | COSSE | Carte_Principale-cache:COSSE | base_V2:TSC_CON1_poignard
 |  | J15 | COSSE | Carte_Principale-cache:COSSE | base_V2:TSC_CON1_poignard
 |  | J16 | COSSE | Carte_Principale-cache:COSSE | base_V2:TSC_CON1_poignard
 |  | J17 | 95009-7441 | Carte_Principale-cache:95009-7441 | Carte_Principale:RJ11-95009-7441 | https://componentsearchengine.com/Datasheets/1/95009-7441.pdf | RJ11 R/A PCB modular jack; w/panel stops Molex 4P4C Right Angle PCB Mount RJ11 Modular Jack Connector 95009 | Molex | 95009-7441 | 538-95009-7441 | https://www.mouser.com/Search/Refine.aspx?Keyword=538-95009-7441
 |  | J18 | 95009-7441 | Carte_Principale-cache:95009-7441 | Carte_Principale:RJ11-95009-7441 | https://componentsearchengine.com/Datasheets/1/95009-7441.pdf | RJ11 R/A PCB modular jack; w/panel stops Molex 4P4C Right Angle PCB Mount RJ11 Modular Jack Connector 95009 | Molex | 95009-7441 | 538-95009-7441 | https://www.mouser.com/Search/Refine.aspx?Keyword=538-95009-7441
 |  | J19 | CONN_01X05 | Carte_Principale-cache:CONN_01X05 | Pin_Headers:Pin_Header_Straight_1x05_Pitch2.54mm
 |  | R1 | 10k | device:R | Resistors_SMD:R_1206_HandSoldering
 |  | R2 | 10k | device:R | Resistors_SMD:R_1206_HandSoldering
 |  | R3 | 1k | device:R | Resistors_SMD:R_1206_HandSoldering
 |  | R4 | 1k | device:R | Resistors_SMD:R_1206_HandSoldering
 |  | R5 | 1k | device:R | Resistors_SMD:R_1206_HandSoldering
 |  | R6 | 1k | device:R | Resistors_SMD:R_1206_HandSoldering
 |  | R7 | 1M | device:R | Resistors_SMD:R_1206_HandSoldering
 |  | R8 | 1M | device:R | Resistors_SMD:R_1206_HandSoldering
 |  | R9 | 10k | device:R | Resistors_SMD:R_1206_HandSoldering
 |  | R10 | 10k | device:R | Resistors_SMD:R_1206_HandSoldering
 |  | R11 | 2019-02-02 | device:R | Resistors_SMD:R_1206_HandSoldering
 |  | R12 | 2019-02-02 | device:R | Resistors_SMD:R_1206_HandSoldering
 |  | R13 | 2019-02-02 | device:R | Resistors_SMD:R_1206_HandSoldering
 |  | R14 | 2019-02-02 | device:R | Resistors_SMD:R_1206_HandSoldering
 |  | R15 | 1K | device:R | Resistors_SMD:R_1206_HandSoldering
 |  | R16 | 1K | device:R | Resistors_SMD:R_1206_HandSoldering
 |  | R17 | 1K | device:R | Resistors_SMD:R_1206_HandSoldering
 |  | U1 | MCP23008 | microchip:MCP23008 | Carte_Principale:SOIC-18
 |  | U2 | 4081 | cmos4000:4081 | base_V2:SM_SO-14
 |  | U3 | DRV8825 | Carte_Principale:DRV8825 | Carte_Principale:DRV8825
 |  | U4 | DRV8825 | Carte_Principale:DRV8825 | Carte_Principale:DRV8825
 |  | U7 | C8051F38C | Carte_Principale:C8051F38C | Carte_Principale:C8051F38C
Collated Components:
Item | Qty | Reference(s) | Value | Empreinte
1 | 1 | BP1 | POUSSOIR_ON | Buttons_Switches_THT:SW_PUSH_6mm
2 | 2 | C1; C2 | 0.47uF | SMD 1206
3 | 6 | C3; C4; C5; C6; C7; C12 | 0.1uF | SMD 1206
4 | 2 | C8; C13 | 100uF | CP_Radial_D5.0mm_P2.00mm
5 | 2 | C9; C10 | 0.01uF | SMD 1206
6 | 1 | C11 | 1uF | SMD 1206
7 | 1 | J1 | Conn_01x08 | Conn_01x08 Male
8 | 1 | J2 | Conn_01x04 | Conn_01x04 Male
9 | 1 | J3 | RJ12 | conn:RJ12
10 | 1 | J4 | Conn_01x06 | Conn_01x06 Male
11 | 1 | J5 | Conn_01x03 | Conn_01x03 Male
12 | 1 | J12 | HEADER_10P | Carte_Principale:HEADER_10P
13 | 4 | J13; J14; J15; J16 | COSSE | Carte_Principale-cache:COSSE
14 | 2 | J17; J18 | RJ11 | RJ11
15 | 1 | J19 | CONN_01X05 | CONN_01X05 Male
16 | 4 | R1; R2; R9; R10 | 10k | SMD 1206
17 | 4 | R3; R4; R5; R6 | 1k | SMD 1206
18 | 2 | R7; R8 | 1M | SMD 1206
19 | 4 | R11; R12; R13; R14 | 2.2 | SMD 1206
20 | 3 | R15; R16; R17 | 1K | SMD 1206
21 | 1 | U1 | MCP23008 | MCP23008 SOIC-18
22 | 1 | U2 | 4081 | CD4081BE SO-14
23 | 2 | U3; U4 | DRV8825
24 | 1 | U7 | C8051F38C

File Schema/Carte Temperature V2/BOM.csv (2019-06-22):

Source: | C:/Users/DIETRICHT_ELEC/Desktop/Diplome_Telescope_Dietrich_V17/Kicad_Telescope_V6/Carte Temperature V2/Carte_Temperature.sch
Date: | 24.05.2019 10:35
Tool: | Eeschema 4.0.7
Generator: | C:/Program Files/KiCad/bin/scripting/plugins/bom_csv_grouped_by_value.py
Component Count: | 52
Individual Components:
Item | Qty | Reference(s) | Value | LibPart | Footprint | Datasheet
 |  | BP1 | POUSSOIR_ON | Carte_Temperature-cache:POUSSOIR_ON | Buttons_Switches_THT:SW_PUSH_6mm
 |  | C1 | 100nF | device:C | Capacitors_SMD:C_1206_HandSoldering
 |  | C11 | 1uF | device:C | Capacitors_SMD:C_1206_HandSoldering
 |  | D1 | D | device:D | Diodes_THT:D_DO-15_P10.16mm_Horizontal
 |  | D2 | D | device:D | Diodes_THT:D_DO-15_P10.16mm_Horizontal
 |  | D3 | D | device:D | Diodes_THT:D_DO-15_P10.16mm_Horizontal
 |  | D4 | D | device:D | Diodes_THT:D_DO-15_P10.16mm_Horizontal
 |  | J1 | Conn_01x03 | conn:Conn_01x03 | Pin_Headers:Pin_Header_Straight_1x03_Pitch2.54mm
 |  | J2 | Conn_01x03 | conn:Conn_01x03 | Pin_Headers:Pin_Header_Straight_1x03_Pitch2.54mm
 |  | J3 | Conn_01x03 | conn:Conn_01x03 | Pin_Headers:Pin_Header_Straight_1x03_Pitch2.54mm
 |  | J4 | Conn_01x03 | conn:Conn_01x03 | Pin_Headers:Pin_Header_Straight_1x03_Pitch2.54mm
 |  | J5 | Conn_01x03 | conn:Conn_01x03 | Pin_Headers:Pin_Header_Straight_1x03_Pitch2.54mm
 |  | J6 | Conn_01x03 | conn:Conn_01x03 | Pin_Headers:Pin_Header_Straight_1x03_Pitch2.54mm
 |  | J7 | Conn_01x03 | conn:Conn_01x03 | Pin_Headers:Pin_Header_Straight_1x03_Pitch2.54mm
 |  | J8 | Conn_01x03 | conn:Conn_01x03 | Pin_Headers:Pin_Header_Straight_1x03_Pitch2.54mm
 |  | J9 | Conn_01x03 | conn:Conn_01x03 | Pin_Headers:Pin_Header_Straight_1x03_Pitch2.54mm
 |  | J10 | Conn_01x02 | conn:Conn_01x02 | Pin_Headers:Pin_Header_Straight_1x02_Pitch2.54mm
 |  | J11 | Conn_01x01 | conn:Conn_01x01 | base_V2:TSC_CON1_poignard
 |  | J12 | HEADER_10P | Carte_Temperature-cache:HEADER_10P | Carte_Temperature:JTAG
 |  | J13 | Conn_01x03 | conn:Conn_01x03 | Pin_Headers:Pin_Header_Straight_1x03_Pitch2.54mm
 |  | J14 | Conn_01x01 | conn:Conn_01x01 | base_V2:TSC_CON1_poignard
 |  | J15 | Conn_01x01 | conn:Conn_01x01 | base_V2:TSC_CON1_poignard
 |  | J16 | Conn_01x01 | conn:Conn_01x01 | base_V2:TSC_CON1_poignard
 |  | J17 | Conn_01x01 | conn:Conn_01x01 | base_V2:TSC_CON1_poignard
 |  | J18 | RCJ-041 | Carte_Temperature:RCJ-041 | Carte_Temperature:CUI_RCJ-041_Graveuse | RCJ-041
 |  | J19 | RCJ-041 | Carte_Temperature:RCJ-041 | Carte_Temperature:CUI_RCJ-041_Graveuse | RCJ-041
 |  | J20 | Conn_01x01 | conn:Conn_01x01 | base_V2:TSC_CON1_poignard
 |  | J21 | Conn_01x01 | conn:Conn_01x01 | base_V2:TSC_CON1_poignard
 |  | J22 | Conn_01x01 | conn:Conn_01x01 | base_V2:TSC_CON1_poignard
 |  | J23 | Conn_01x01 | conn:Conn_01x01 | base_V2:TSC_CON1_poignard
 |  | J24 | RCJ-041 | Carte_Temperature:RCJ-041 | Carte_Temperature:CUI_RCJ-041_Graveuse | RCJ-041
 |  | J25 | RCJ-041 | Carte_Temperature:RCJ-041 | Carte_Temperature:CUI_RCJ-041_Graveuse | RCJ-041
 |  | J26 | Conn_01x01 | conn:Conn_01x01 | base_V2:TSC_CON1_poignard
 |  | J27 | Conn_01x01 | conn:Conn_01x01 | base_V2:TSC_CON1_poignard
 |  | J28 | Conn_01x01 | conn:Conn_01x01 | base_V2:TSC_CON1_poignard
 |  | J29 | Conn_01x01 | conn:Conn_01x01 | base_V2:TSC_CON1_poignard
 |  | J30 | Conn_01x01 | conn:Conn_01x01 | base_V2:TSC_CON1_poignard
 |  | Q1 | IRL3705 | Carte_Temperature:IRL3705 | Carte_Temperature:TO254P1052X465X1989-3-IRL3705
 |  | Q2 | IRL3705 | Carte_Temperature:IRL3705 | Carte_Temperature:TO254P1052X465X1989-3-IRL3705
 |  | Q3 | IRL3705 | Carte_Temperature:IRL3705 | Carte_Temperature:TO254P1052X465X1989-3-IRL3705
 |  | Q4 | IRL3705 | Carte_Temperature:IRL3705 | Carte_Temperature:TO254P1052X465X1989-3-IRL3705
 |  | R1 | 18k | device:R | Resistors_SMD:R_1206_HandSoldering
 |  | R2 | 18k | device:R | Resistors_SMD:R_1206_HandSoldering
 |  | R3 | 18k | device:R | Resistors_SMD:R_1206_HandSoldering
 |  | R4 | 18k | device:R | Resistors_SMD:R_1206_HandSoldering
 |  | R5 | 1k | device:R | Resistors_SMD:R_1206_HandSoldering
 |  | R6 | 1k | device:R | Resistors_SMD:R_1206_HandSoldering
 |  | R15 | 1K | device:R | Resistors_SMD:R_1206_HandSoldering
 |  | R16 | 1K | device:R | Resistors_SMD:R_1206_HandSoldering
 |  | R17 | 1K | device:R | Resistors_SMD:R_1206_HandSoldering
 |  | U1 | EEH210 | Carte_Temperature:EEH210 | Carte_Temperature:EEH210_1.5mm
 |  | U7 | C8051F38C | Carte_Temperature-cache:C8051F38C | Carte_Temperature:C8051F38C
Collated Components:
Item | Qty | Reference(s) | Value | LibPart | Footprint | Datasheet
1 | 1 | BP1 | POUSSOIR_ON | Carte_Temperature-cache:POUSSOIR_ON | Buttons_Switches_THT:SW_PUSH_6mm
2 | 1 | C1 | 100nF | device:C | Capacitors_SMD:C_1206_HandSoldering
3 | 1 | C11 | 1uF | device:C | Capacitors_SMD:C_1206_HandSoldering
4 | 4 | D1; D2; D3; D4 | D | device:D | Diodes_THT:D_DO-15_P10.16mm_Horizontal
5 | 10 | J1; J2; J3; J4; J5; J6; J7; J8; J9; J13 | Conn_01x03 | conn:Conn_01x03 | Pin_Headers:Pin_Header_Straight_1x03_Pitch2.54mm
6 | 1 | J10 | Conn_01x02 | conn:Conn_01x02 | Pin_Headers:Pin_Header_Straight_1x02_Pitch2.54mm
7 | 14 | J11; J14; J15; J16; J17; J20; J21; J22; J23; J26; J27; J28; J29; J30 | Conn_01x01 | conn:Conn_01x01 | base_V2:TSC_CON1_poignard
8 | 1 | J12 | HEADER_10P | Carte_Temperature-cache:HEADER_10P | Carte_Temperature:JTAG
9 | 4 | J18; J19; J24; J25 | RCJ-041 | Carte_Temperature:RCJ-041 | Carte_Temperature:CUI_RCJ-041_Graveuse | RCJ-041
10 | 4 | Q1; Q2; Q3; Q4 | IRL3705 | Carte_Temperature:IRL3705 | Carte_Temperature:TO254P1052X465X1989-3-IRL3705
11 | 4 | R1; R2; R3; R4 | 18k | device:R | Resistors_SMD:R_1206_HandSoldering
12 | 2 | R5; R6 | 1k | device:R | Resistors_SMD:R_1206_HandSoldering
13 | 3 | R15; R16; R17 | 1K | device:R | Resistors_SMD:R_1206_HandSoldering
14 | 1 | U1 | EEH210 | Carte_Temperature:EEH210 | Carte_Temperature:EEH210_1.5mm
15 | 1 | U7 | C8051F38C | Carte_Temperature-cache:C8051F38C | Carte_Temperature:C8051F38C

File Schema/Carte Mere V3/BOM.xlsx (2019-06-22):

Source: | C:/Users/DIETRICHT_ELEC/Desktop/Diplome_Telescope_Dietrich_V17/Kicad_Telescope_V6/Carte Mere V3/Carte_Mere.sch
Date: | 2019-05-24 08:18
Tool: | Eeschema 4.0.7
Generator: | C:/Program Files/KiCad/bin/scripting/plugins/bom_csv_grouped_by_value.py
Component Count: | 43
Individual Components:
Item | Qty | Reference(s) | Value | LibPart | Footprint | Datasheet
 |  | C1 | 100uF | device:C | Capacitors_THT:CP_Radial_D5.0mm_P2.00mm
 |  | J1 | Jack-DC | conn:Jack-DC | Carte Mere:JACK_ALIM
 |  | J2 | Conn_01x03_Male | conn:Conn_01x03_Male | Pin_Headers:Pin_Header_Straight_1x03_Pitch2.54mm
 |  | J3 | Raspberry_Pi_2_3 | conn:Raspberry_Pi_2_3 | Carte Mere:RaspberryPI3_V2
 |  | J4 | Conn_01x03_Male | conn:Conn_01x03_Male | Pin_Headers:Pin_Header_Straight_1x03_Pitch2.54mm
 |  | J5 | Conn_01x05 | conn:Conn_01x05 | Pin_Headers:Pin_Header_Straight_1x05_Pitch2.54mm
 |  | J6 | Conn_01x05 | conn:Conn_01x05 | Pin_Headers:Pin_Header_Straight_1x05_Pitch2.54mm
 |  | J7 | Conn_01x05 | conn:Conn_01x05 | Pin_Headers:Pin_Header_Straight_1x05_Pitch2.54mm
 |  | J8 | Conn_01x03_Male | conn:Conn_01x03_Male | Pin_Headers:Pin_Header_Straight_1x03_Pitch2.54mm
 |  | J9 | Conn_01x03_Male | conn:Conn_01x03_Male | Pin_Headers:Pin_Header_Straight_1x03_Pitch2.54mm
 |  | J10 | Conn_01x03_Male | conn:Conn_01x03_Male | Pin_Headers:Pin_Header_Straight_1x03_Pitch2.54mm
 |  | J11 | Conn_01x03_Male | conn:Conn_01x03_Male | Pin_Headers:Pin_Header_Straight_1x03_Pitch2.54mm
 |  | J12 | Conn_01x03_Male | conn:Conn_01x03_Male | Pin_Headers:Pin_Header_Straight_1x03_Pitch2.54mm
 |  | J13 | Conn_01x03_Male | conn:Conn_01x03_Male | Pin_Headers:Pin_Header_Straight_1x03_Pitch2.54mm
 |  | J14 | Conn_01x03_Male | conn:Conn_01x03_Male | Pin_Headers:Pin_Header_Straight_1x03_Pitch2.54mm
 |  | J15 | Conn_01x02 | conn:Conn_01x02 | Carte Mere:Pin_alimentation
 |  | J16 | Conn_01x01 | conn:Conn_01x01 | Carte Mere:TSC_CON1_poignard
 |  | J17 | Conn_01x01 | conn:Conn_01x01 | Carte Mere:TSC_CON1_poignard
 |  | J18 | Conn_01x04_Male | conn:Conn_01x04_Male | Pin_Headers:Pin_Header_Straight_1x04_Pitch2.54mm
 |  | J19 | Conn_01x01 | conn:Conn_01x01 | Carte Mere:TSC_CON1_poignard
 |  | J20 | Conn_01x01 | conn:Conn_01x01 | Carte Mere:TSC_CON1_poignard
 |  | J21 | Conn_01x01 | conn:Conn_01x01 | Carte Mere:TSC_CON1_poignard
 |  | J22 | Conn_01x01 | conn:Conn_01x01 | Carte Mere:TSC_CON1_poignard
 |  | J23 | Conn_01x01 | conn:Conn_01x01 | Carte Mere:TSC_CON1_poignard
 |  | J24 | Conn_01x01 | conn:Conn_01x01 | Carte Mere:TSC_CON1_poignard
 |  | J25 | Conn_01x01 | conn:Conn_01x01 | Carte Mere:TSC_CON1_poignard
 |  | JP1 | Jumper | device:Jumper | Carte Mere:Pin_alimentation
 |  | R1 | 10k | device:R | Resistors_SMD:R_1206_HandSoldering
 |  | R2 | 10k | device:R | Resistors_SMD:R_1206_HandSoldering
 |  | R3 | 10k | device:R | Resistors_SMD:R_1206_HandSoldering
 |  | R4 | 10k | device:R | Resistors_SMD:R_1206_HandSoldering
 |  | R5 | 10k | device:R | Resistors_SMD:R_1206_HandSoldering
 |  | R6 | 10k | device:R | Resistors_SMD:R_1206_HandSoldering
 |  | R7 | 10k | device:R | Resistors_SMD:R_1206_HandSoldering
 |  | R8 | 10k | device:R | Resistors_SMD:R_1206_HandSoldering
 |  | R9 | 10k | device:R | Resistors_SMD:R_1206_HandSoldering
 |  | R10 | 10k | device:R | Resistors_SMD:R_1206_HandSoldering
 |  | R11 | 10k | device:R | Resistors_SMD:R_1206_HandSoldering
 |  | R12 | 10k | device:R | Resistors_SMD:R_1206_HandSoldering
 |  | R13 | 10k | device:R | Resistors_SMD:R_1206_HandSoldering
 |  | U1 | Carte_Moteur | Carte_Mere:Carte_Moteur | Carte Mere:Carte_Moteur_V2
 |  | U2 | LM2576 | Carte_Mere:LM2576 | Carte Mere:Alimentation_V2
 |  | U3 | Carte_Temperature | Carte_Mere:Carte_Temperature | Carte Mere:Carte_Temperature
Collated Components:
Item | Qty | Reference(s) | Value | Empreinte
1 | 1 | C1 | 100uF | CP_Radial_D5.0mm_P2.00mm
2 | 1 | J1 | Jack-DC
3 | 9 | J2; J4; J8; J9; J10; J11; J12; J13; J14 | Conn_01x03_Male
4 | 1 | J3 | Conn_02x20_Femelle | Raspberry Pi 3
5 | 3 | J5; J6; J7 | Conn_01x05_Male
6 | 1 | J15 | Conn_01x02_Male
7 | 9 | J16; J17; J19; J20; J21; J22; J23; J24; J25 | Cosse Poignard
8 | 1 | J18 | Conn_01x04_Male
9 | 2 | JP1 | Conn_01x03_Male
10 | 13 | R1; R2; R3; R4; R5; R6; R7; R8; R9; R10; R11; R12; R13 | 10k | SMD 1206
11 | 1 | U1 | Carte Moteur | Carte Moteur
12 | 1 | U2 | LM2576 | LM2576
13 | 1 | U3 | Carte Temperature | Carte Temperature
14 | 5 | U3,U2 | Conn_01x02_Femelle
15 | 11 | U3,U1 | Conn_01x03_Femelle
16 | 1 | U1 | Conn_01x04_Femelle
17 | 1 | U1 | Conn_01x05_Femelle
18 | 1 | U1 | Conn_01x06_Femelle
19 | 1 | U1 | Conn_01x08_Femelle

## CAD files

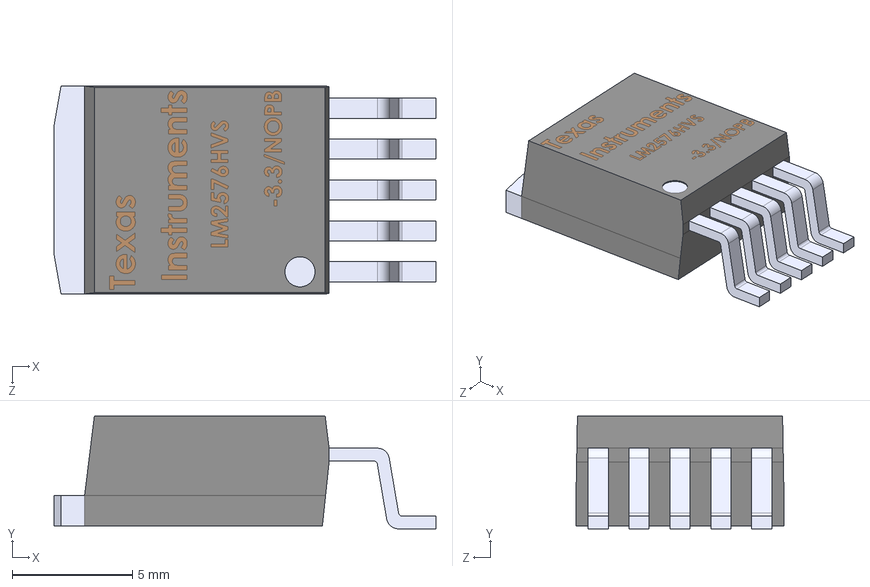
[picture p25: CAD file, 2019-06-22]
Schema/Charge_active_Dietrich_V2/3D/D2PAK_LM2576_MODEL.STEP
15.9 x 4.68 x 8.64 mm
D2PAK_LM2576_PIN x 5
D2PAK_LM2576_BODY

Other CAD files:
Master_Telescope/Objects/Master_Telescope V3.obj
Slave_Telescope/Objects/Master_Telescope.obj
Slave_Telescope/Objects/Slave_Telescope.obj
Master_Telescope/Objects/Master_Telescope_V2.obj
Master_Telescope/Objects/Master_Telescope.obj

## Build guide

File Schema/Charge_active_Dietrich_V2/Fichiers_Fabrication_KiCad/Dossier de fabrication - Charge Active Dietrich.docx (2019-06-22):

Projet / produit : | Charge Active
Description :
Quantités : | 1 | pièce
| _ | pièces / lot de fabrication
| _ | pièces / an

Circuit :

Nom : | Charge Active – Régulateur a découpage
Numéro : | ND (Non Disponible)
Révision : | 0
Date de création : | 17.09.2018 | Auteur : | Tanguy Dietrich

Historique des modifications :

Rév. | Date | Auteur | Détails des modifications
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
Spécification du PCB :

Nature du matériel isolant : [ ] Bakélite [ ] FR-2 [ ] ___

[ ] Epoxy [x] FR-4 [ ] ___

[ ] Autre : ___

Epaisseur du PCB : [ ] 0.5 mm [ ] 0.8 mm [ ] 1.0 mm [ ] 1.2 mm

[x] 1.6 mm [ ] 2.0 mm [ ] autre : _ mm

Nombre de couches : [ ] Simple face

[x] Double face

[ ] Multicouches, nombre de couches = X

Epaisseur des couches cuivre :

Externe [x] 18 µ [ ] 35 µ [ ] 75 µ [ ] 105 µ [ ] autre : _

Interne [ ] 18 µ [ ] 35 µ [ ] 75 µ [ ] 105 µ [ ] autre : _

Largeur minimum des pistes : 0.508 mm / 20m inch

Largeur minimum entre pistes : 0.254 mm / 10m inch

Liste des documents :

[x] | Schéma électrique | Page 3
[x] | Liste du matériel | Page 3
[x] | Dimensions du PCB | Page 4
[x] | Plan de perçage | Page 5
[x] | Plan d'implantation dessous | Page 6
[x] | Plan d'implantation dessus | Page 6
[x] | Print : vue de dessous | Page 7
[x] | Print : vue de dessus | Page 7
[x] | Points tests | Page 8
[ ] | Fichier Gerber | ___

Schéma électrique :

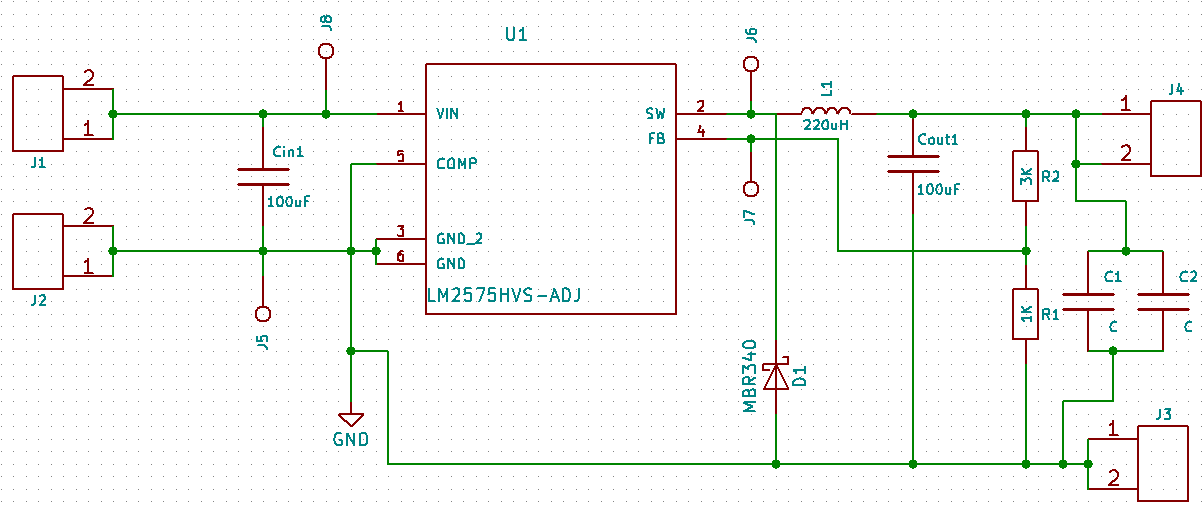
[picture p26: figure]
Schema

Liste du matériel :

Références | Composant | Référence fabricant | Quantité | Pu [CHF] | Ptot [CHF]
J1…J4 | Connecteur 2 poles | | 4
Cin1, Cout1 | Condensateur 100uF 25VDC | | 2
J5…J8 | Cosse | | 4
C1 | Condensateur SMD 1206 100nF | | 1
C2 | Condensateur SMD 1206 1nF | | 1
U1 | LM2575 | | 1
R1 | SMD 1206 1KΩ | | 1
R2 | SMD 1206 3KΩ | | 1
D1 | MBR340 | | 1
L1 | 220uH SMD | | 1
Prix total = | | | | [CHF]

Dimensions de la carte :

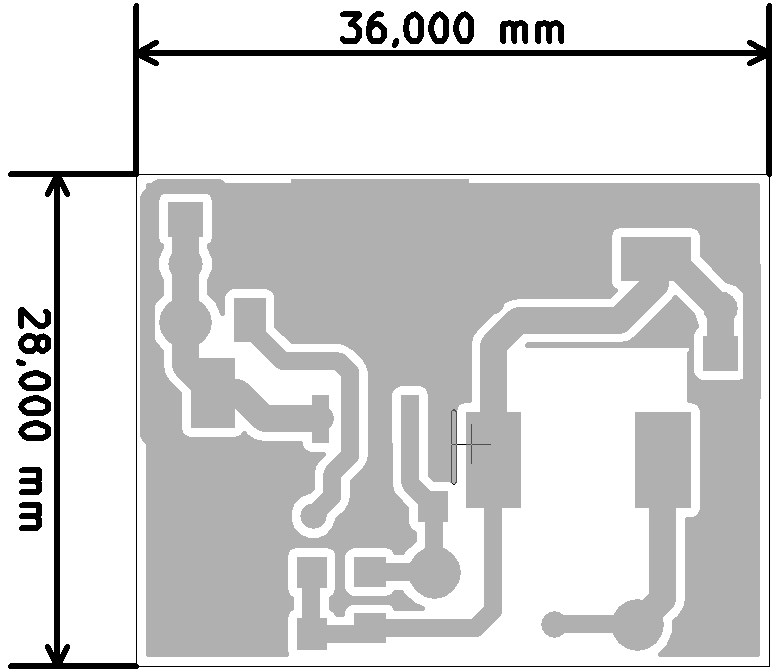
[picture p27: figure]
Dimension

Plan de perçage :

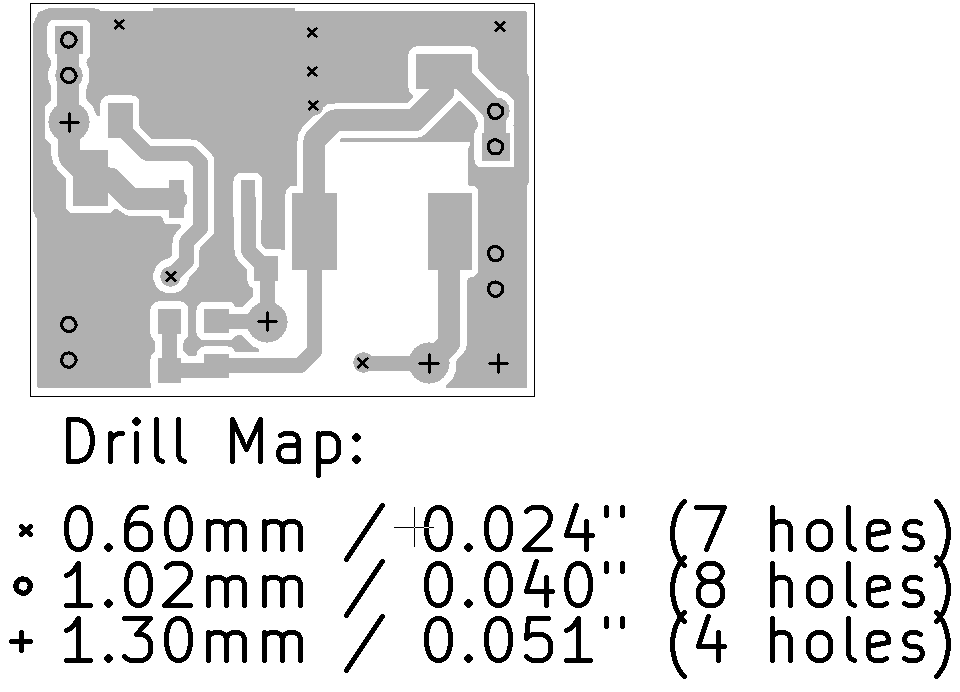
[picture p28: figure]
Drill Map
Bottom

Plan d'implantation dessous :

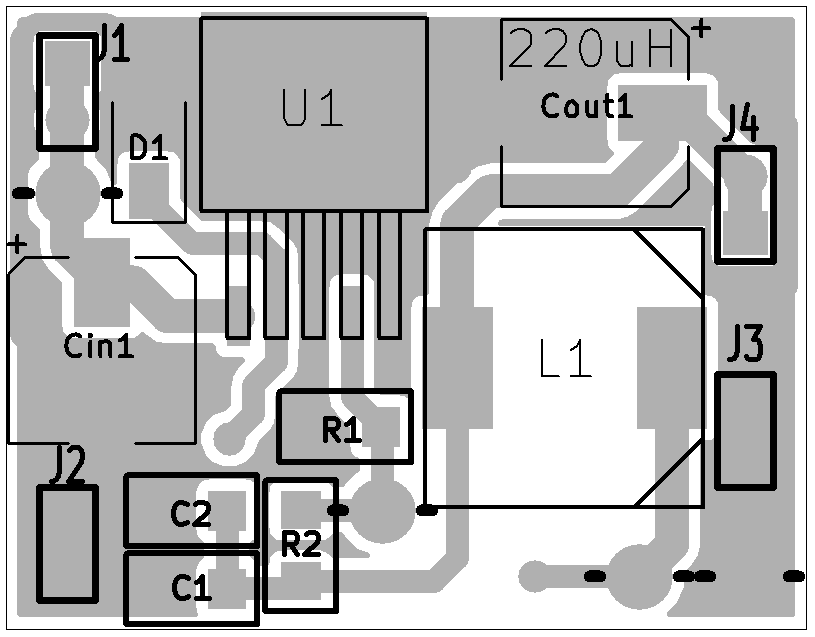
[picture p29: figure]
Top_Composant

Plan d'implantation dessus :

Print : vue de dessous :

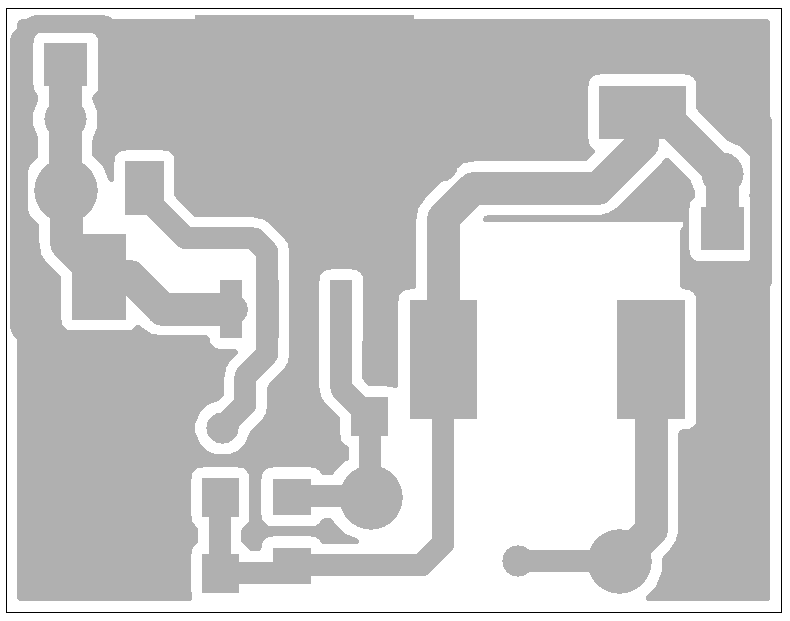
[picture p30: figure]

Print : vue de dessus :

Points tests :


république et canton de genève département de l’instruction PUBLIQUE, DE LA CULTURE ET DU SPORT enseignement secondaire ii postobligatoire Centre de formation professionnelle technique CAO Dossier de fabrication

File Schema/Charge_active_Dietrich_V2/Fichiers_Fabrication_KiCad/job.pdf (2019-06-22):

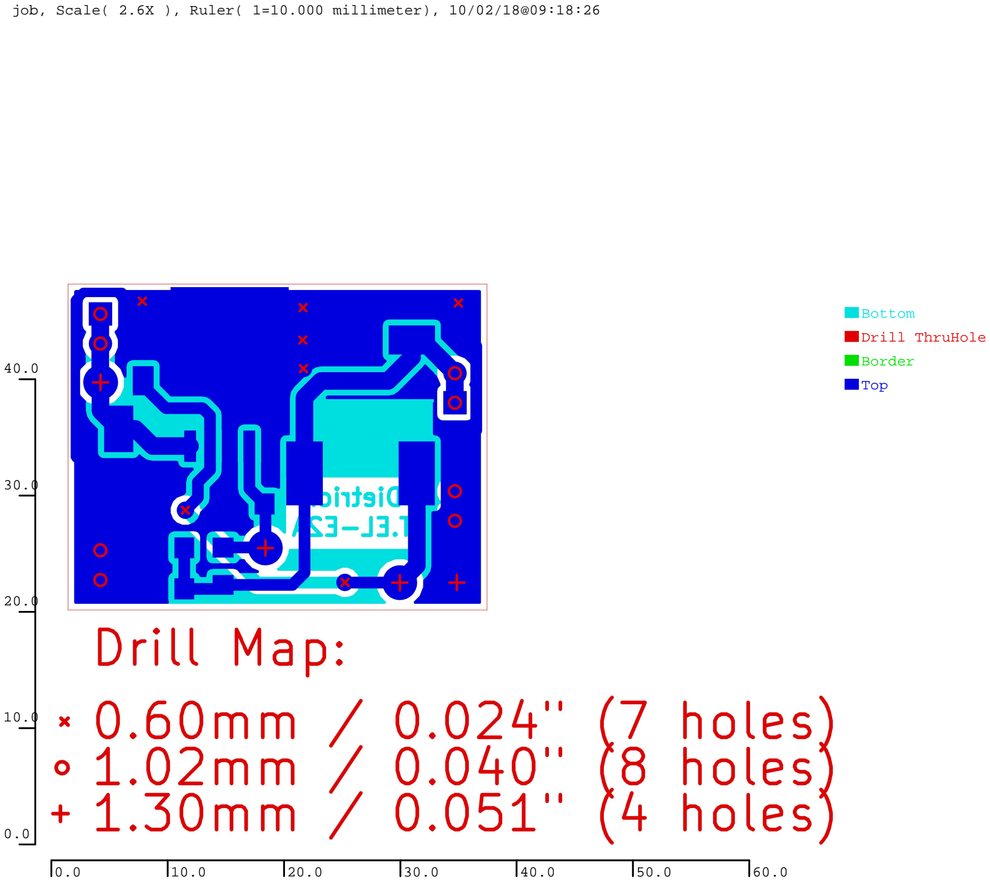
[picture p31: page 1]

job, Scale( 2.6X ), Ruler( 1=10.000 millimeter), 10/02/18@09:18:26

Bottom
Drill ThruHole
Border
Top

0.0

10.0

20.0

30.0

40.0

0.0 | 10.0 | 20.0 | 30.0 | 40.0 | 50.0 | 60.0

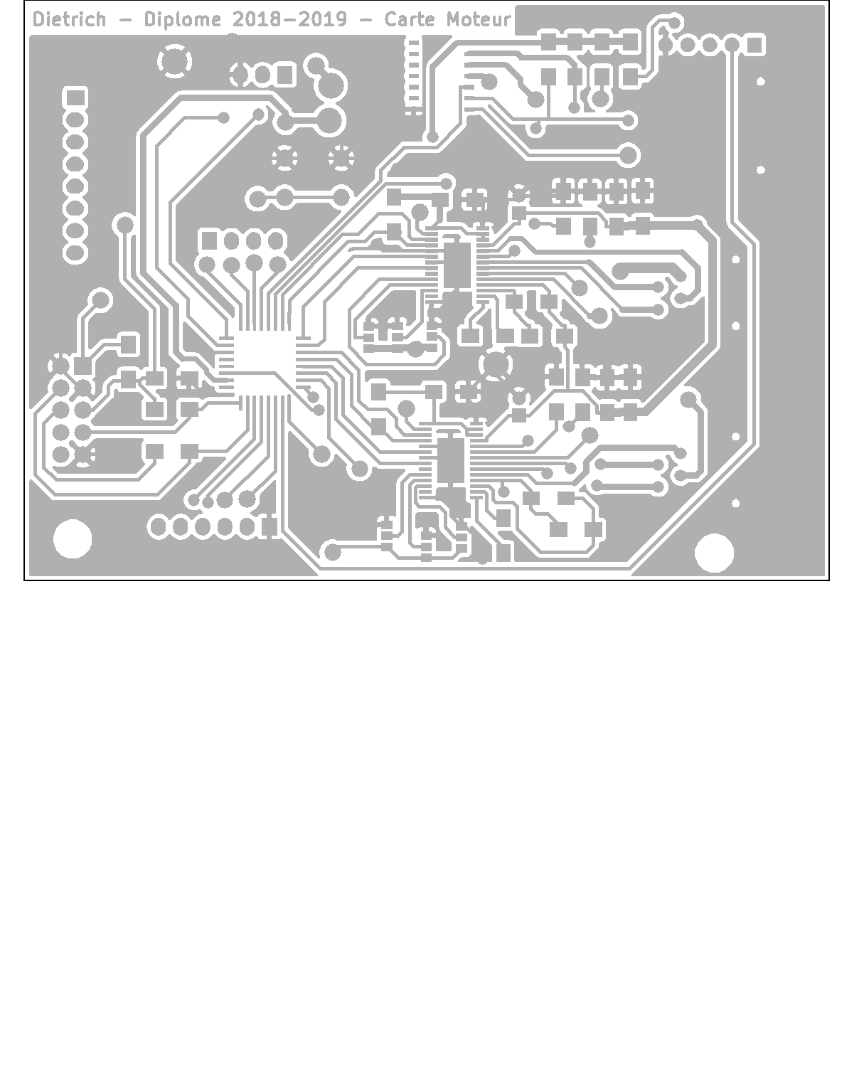
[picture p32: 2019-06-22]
Schema/Carte Moteur V2/Image Dossier Fabrication/Dessus.png

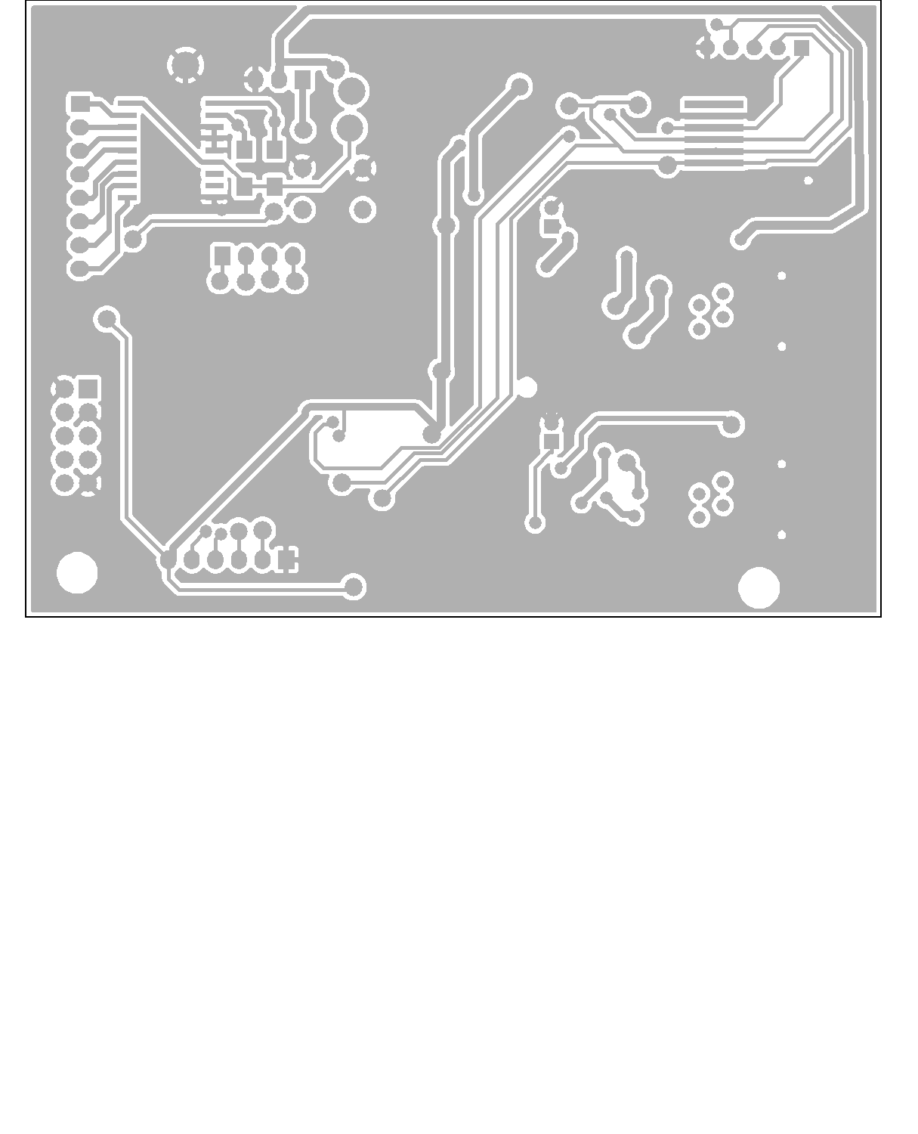
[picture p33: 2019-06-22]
Schema/Carte Moteur V2/Image Dossier Fabrication/Dessous.png

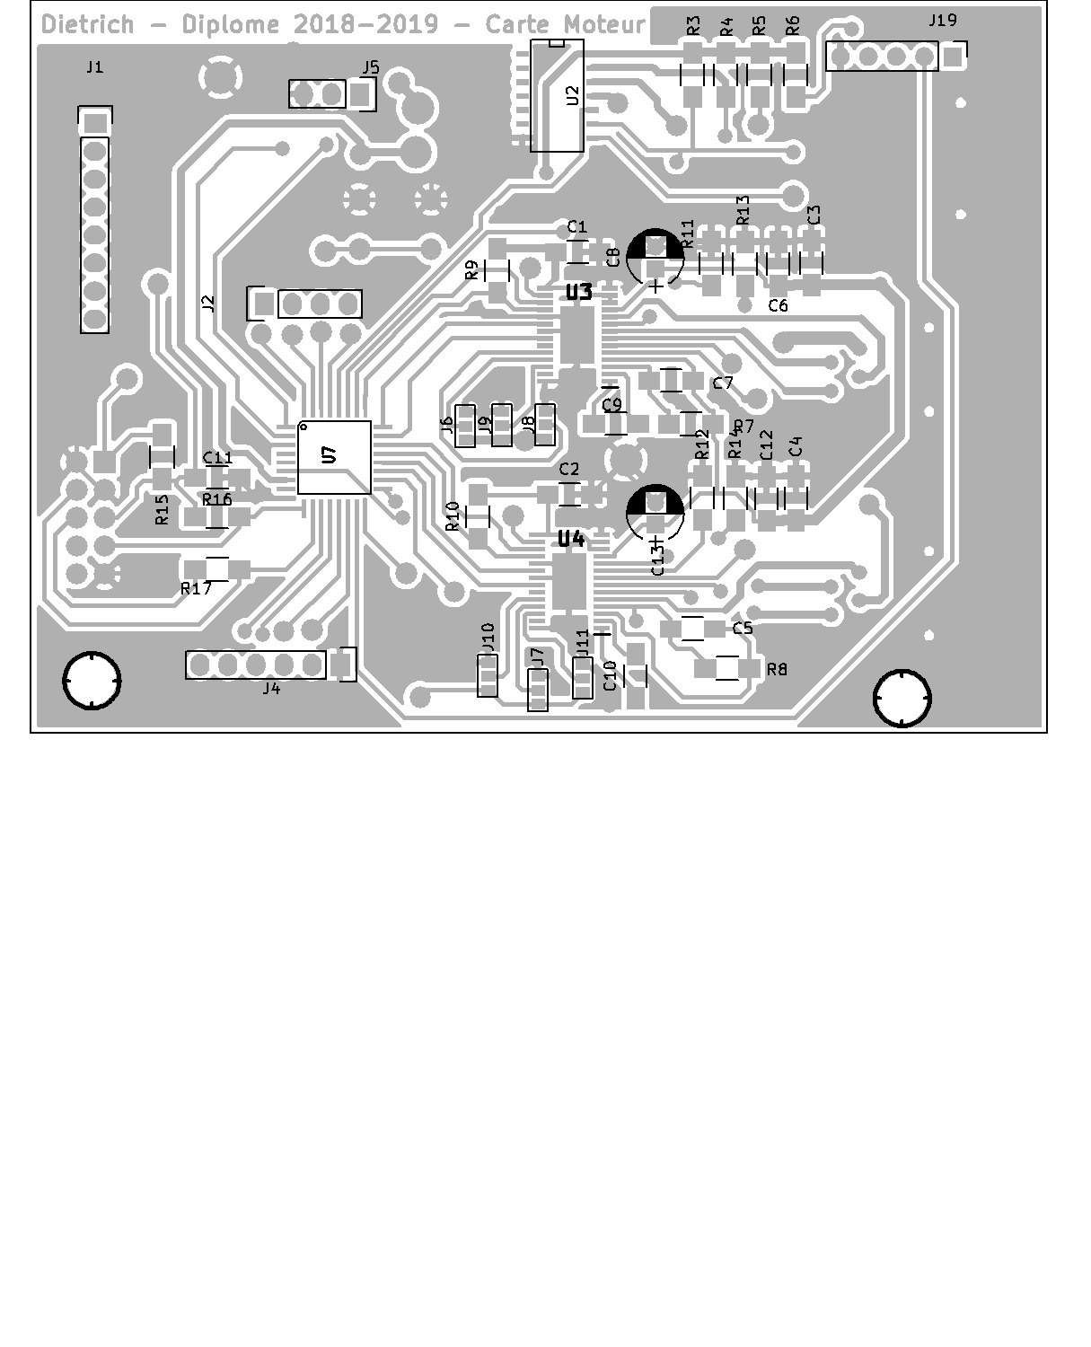
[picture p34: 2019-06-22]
Schema/Carte Moteur V2/Image Dossier Fabrication/Implantation Dessus.png

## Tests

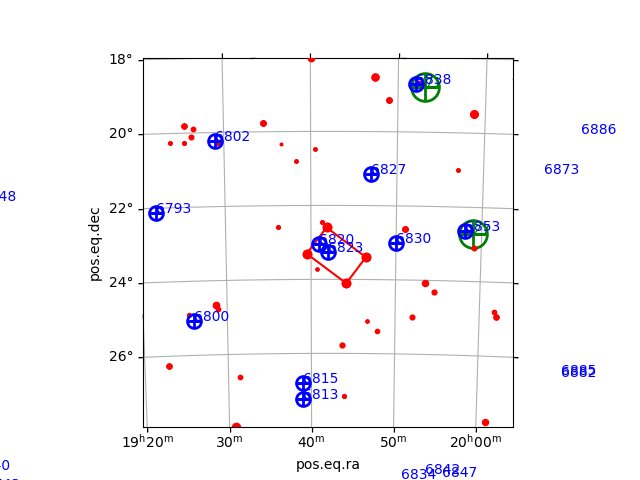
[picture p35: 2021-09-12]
Web_Telescope/Python_Plate_Solve/sky_plot_result.png

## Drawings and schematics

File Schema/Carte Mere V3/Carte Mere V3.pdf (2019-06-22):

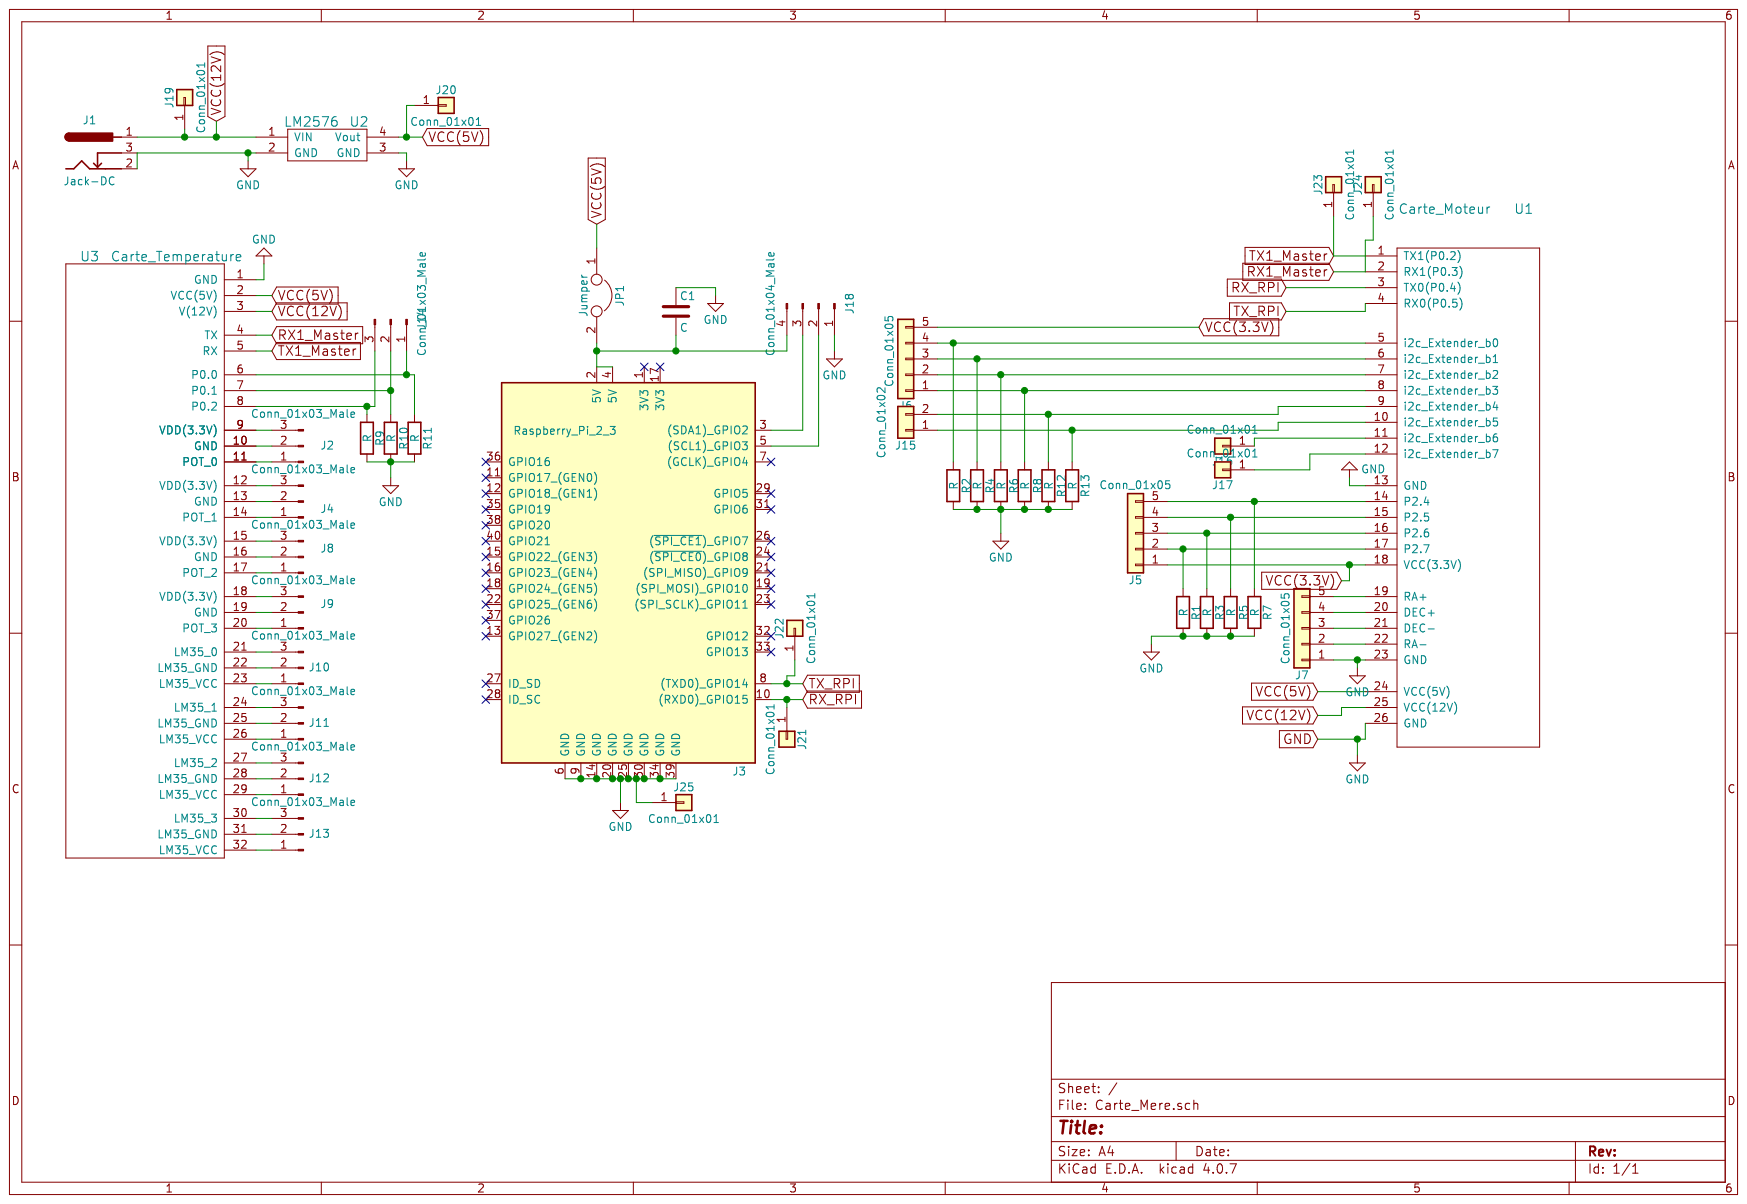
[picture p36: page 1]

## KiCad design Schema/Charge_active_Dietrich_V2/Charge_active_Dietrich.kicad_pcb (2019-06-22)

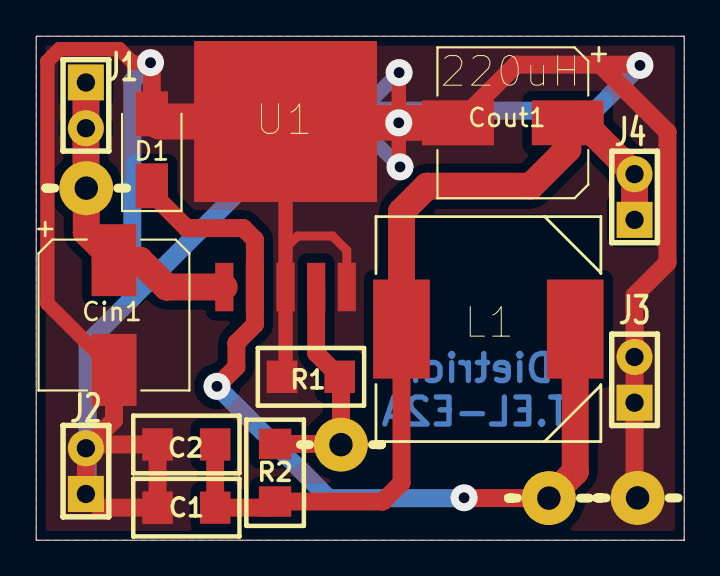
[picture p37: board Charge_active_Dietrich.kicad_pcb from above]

Board: 2 copper layers, 36.0 x 28.0 mm, 17 parts (0 on the bottom side), 5 nets.

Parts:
C1, C2: C; SM_C_1206
Cin1: 100uF; CP_Elec_8x10
Cout1: 100uF; CP_Elec_8x10
D1: MBR340; D_SMA
J1, J2, J3, J4: CON2; TSC_CON2_SIL
J5, J6, J7, J8: CON1; TSC_CON1_poignard
L1: 220uH; INDM125125X800N
R1: 1K; SM_R_1206
R2: 3K; SM_R_1206
U1: LM2575HVS-ADJ; TO170P1435X457-6N

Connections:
GND: C1.2, C2.2, Cin1.2, Cout1.2, D1.2, J2.1, J2.2, J3.1, J3.2, J5.1, R1.2, U1.3, U1.5, U1.6
unnamed: C1.1, C2.1, Cout1.1, J4.1, J4.2, L1.2, R2.1
unnamed: Cin1.1, J1.1, J1.2, J8.1, U1.1
unnamed: D1.1, J6.1, L1.1, U1.2
unnamed: J7.1, R1.1, R2.2, U1.4

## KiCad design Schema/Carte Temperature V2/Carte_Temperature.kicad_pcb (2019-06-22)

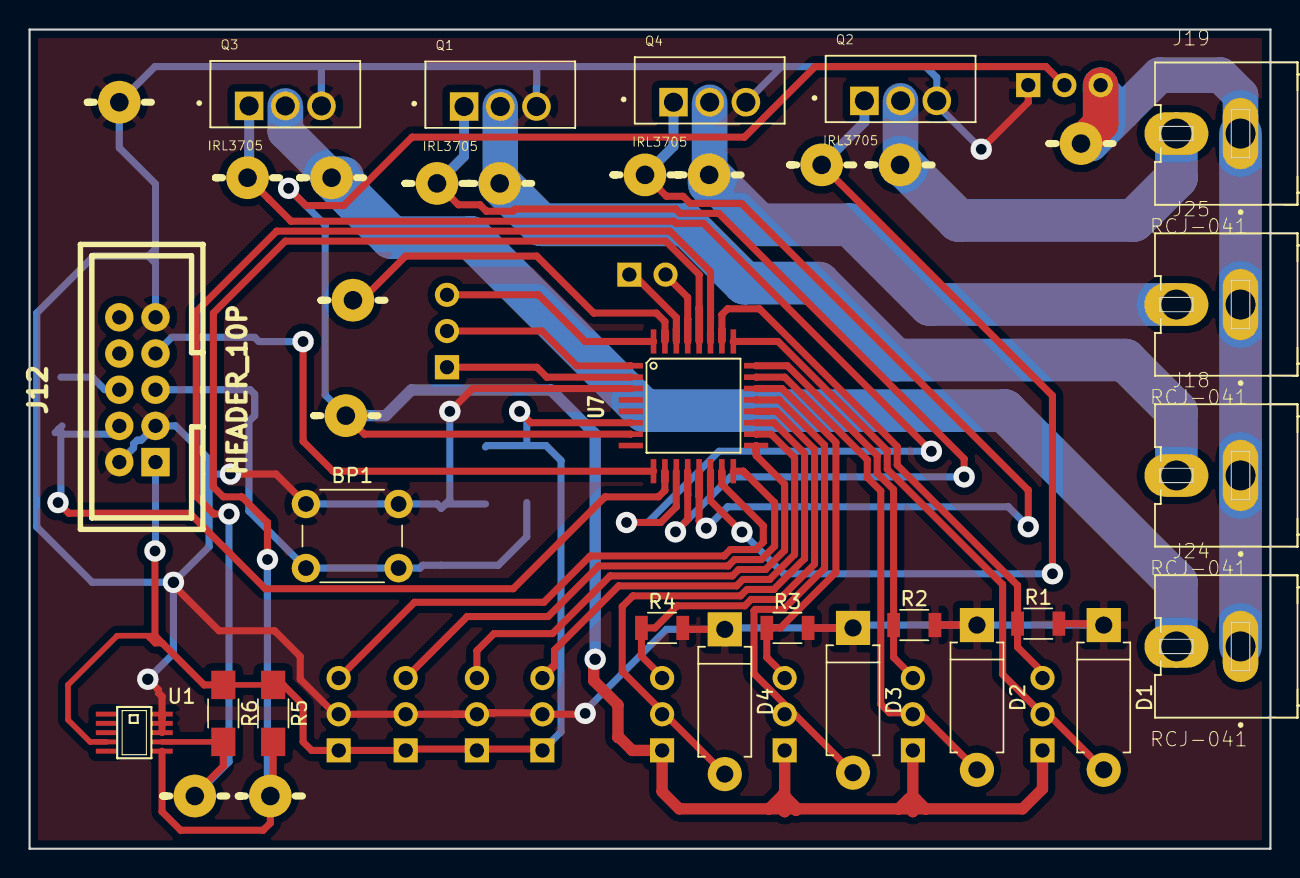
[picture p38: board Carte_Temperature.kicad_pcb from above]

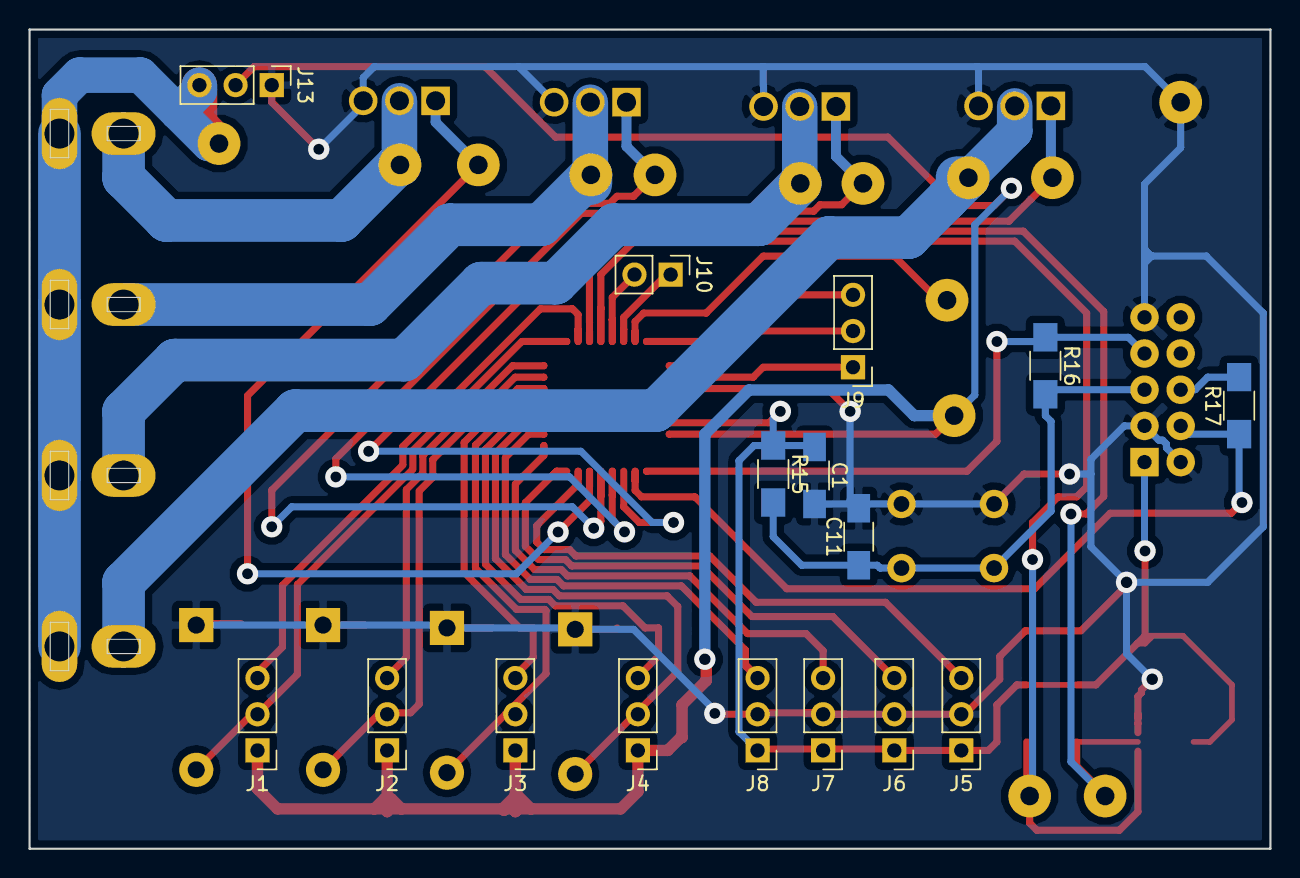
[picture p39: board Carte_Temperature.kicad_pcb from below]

Board: 2 copper layers, 87.1 x 57.5 mm, 52 parts (16 on the bottom side), 36 nets.

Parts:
BP1: POUSSOIR_ON; SW_PUSH_6mm
C1: C; C_1206_HandSoldering
C11: 1uF; C_1206_HandSoldering
D1, D2, D3, D4: D; D_DO-15_P10.16mm_Horizontal
J1, J2, J3, J4, J5, J6, J7, J8, J9, J13: Conn_01x03; Pin_Header_Straight_1x03_Pitch2.54mm
J10: Conn_01x02; Pin_Header_Straight_1x02_Pitch2.54mm
J11, J14, J15, J16, J17, J20, J21, J22, J23, J26, J27, J28, J29, J30: Conn_01x01; TSC_CON1_poignard
J12: HEADER_10P; JTAG
J18, J19, J24, J25: RCJ-041; CUI_RCJ-041_Graveuse
Q1, Q2, Q3, Q4: IRL3705; TO254P1052X465X1989-3-IRL3705
R1, R2, R3, R4: 18k; R_1206
R5, R6: R; R_1206_HandSoldering
R15, R16, R17: 1K; R_1206_HandSoldering
U1: EEH210; EEH210_1.5mm
U7: C8051F38C

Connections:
/C8051F38C/P0.0: J9.1, U7.2
/C8051F38C/P0.1: J9.2, U7.1
/C8051F38C/P0.2: J9.3, U7.32
/C8051F38C/P0.3: J11.1, U7.31
/C8051F38C/P0.4: J10.1, U7.30
/C8051F38C/P0.5: J10.2, U7.29
/C8051F38C/P0.6: J26.1, R5.2, U1.6, U7.28
/C8051F38C/P0.7: J27.1, R6.2, U1.7, U7.27
GND: BP1.1, C1.2, C11.2, D1.1, D2.1, D3.1, D4.1, J5.2, J6.2, J7.2, J8.2, J12.2, J12.3, J12.9, J13.1, J30.1, Q1.3, Q2.3, Q3.3, Q4.3, R1.2, R2.2, R3.2, R4.2, U1.8, U1.9, U1.10, U7.3
LM35_0_NEG: D1.2, J1.2, U7.25
LM35_0_POS: J1.3, R1.1, U7.26
LM35_1_NEG: D2.2, J2.2, U7.23
LM35_1_POS: J2.3, R2.1, U7.24
LM35_2_NEG: D3.2, J3.2, U7.21
LM35_2_POS: J3.3, R3.1, U7.22
LM35_3_NEG: D4.2, J4.2, U7.19
LM35_3_POS: J4.3, R4.1, U7.20
unnamed: BP1.2, C11.1, J12.5, R15.2, R16.2
unnamed: J12.4, R17.1, U7.10
unnamed: J12.6, R17.2
unnamed: J12.7, R16.1, U7.9
unnamed: J16.1, J18.2, Q1.2
unnamed: J17.1, J19.2, Q2.2
unnamed: J22.1, J24.2, Q3.2
unnamed: J23.1, J25.2, Q4.2
PCA0: J15.1, Q2.1, U7.14
PCA1: J21.1, Q4.1, U7.13
PCA2: J14.1, Q1.1, U7.12
PCA3: J20.1, Q3.1, U7.11
POT_0: J8.3, U7.18
POT_1: J7.3, U7.17
POT_2: J6.3, U7.16
POT_3: J5.3, U7.15
V(12V): J13.3, J18.1, J19.1, J24.1, J25.1, J29.1
VCC(5V): J1.1, J2.1, J3.1, J4.1, J13.2, J28.1, U7.7
VDD(3.3V): C1.1, J5.1, J6.1, J7.1, J8.1, J12.1, R5.1, R6.1, R15.1, U1.4, U7.6

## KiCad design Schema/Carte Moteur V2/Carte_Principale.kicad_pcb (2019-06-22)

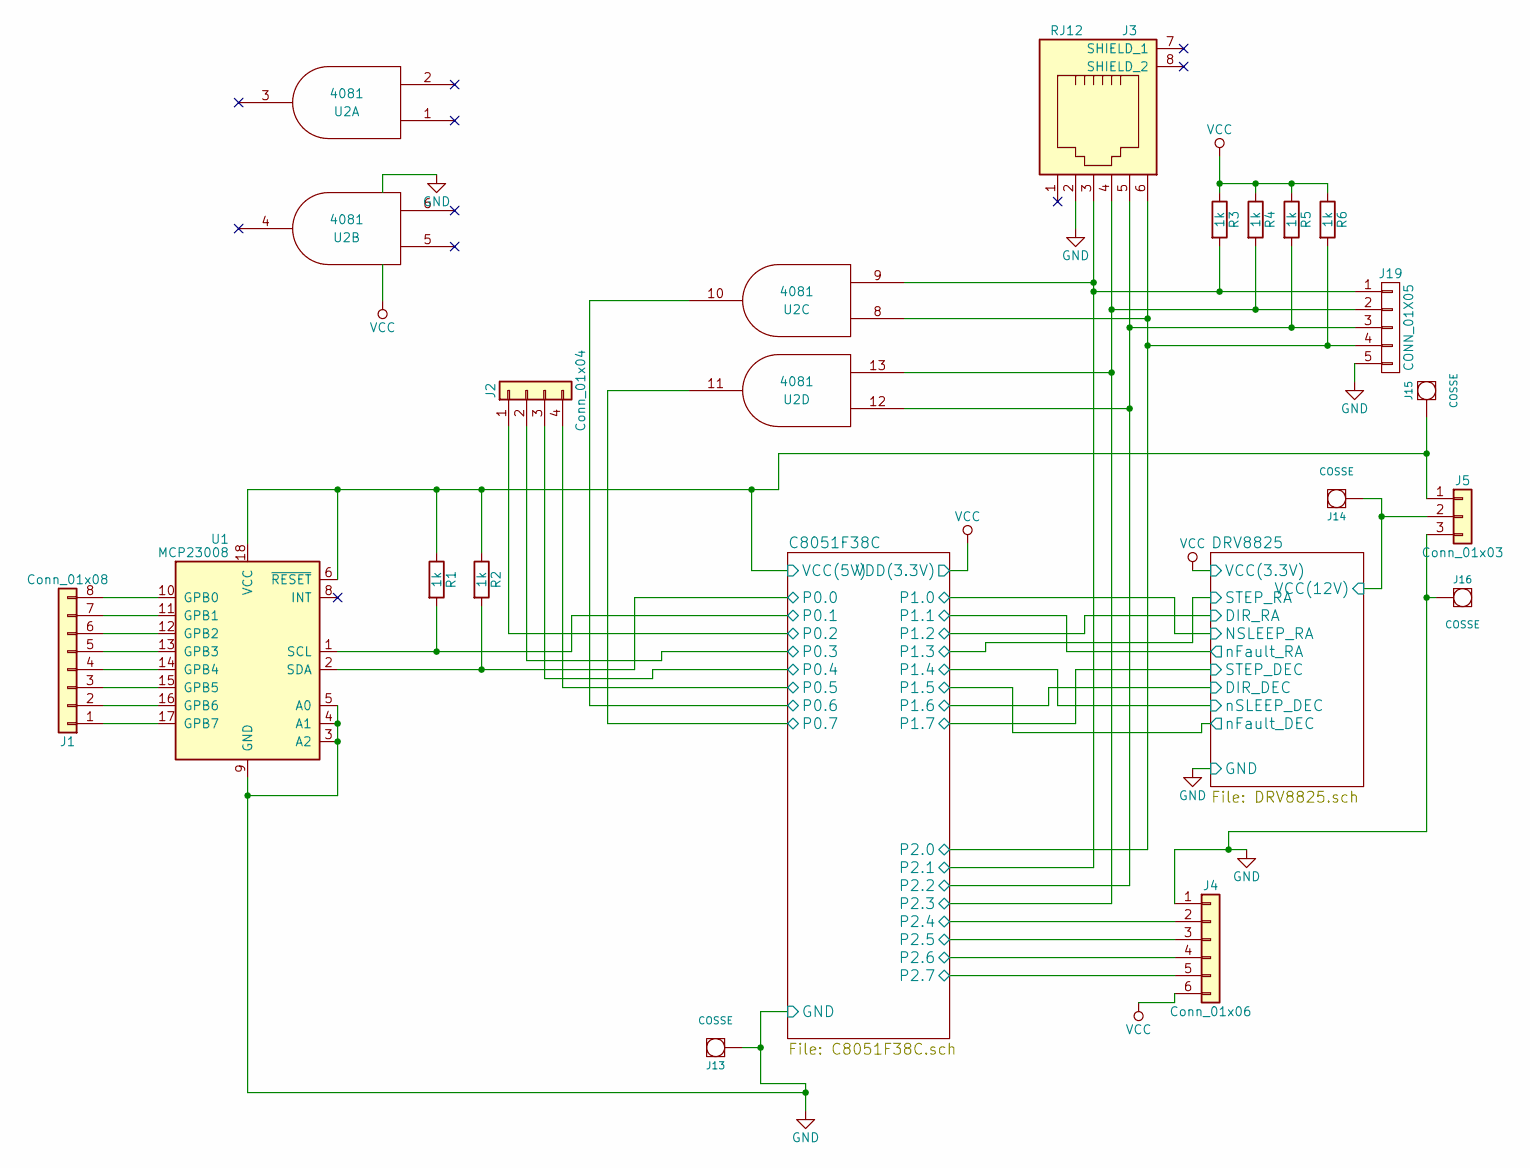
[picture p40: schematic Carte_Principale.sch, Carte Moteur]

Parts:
J1: Conn_01x08; Pin_Header_Straight_1x08
J2: Conn_01x04; Pin_Header_Straight_1x04
J3: RJ12
J4: Conn_01x06; Pin_Header_Straight_1x06
J5: Conn_01x03; Pin_Header_Straight_1x03
J13, J14, J15, J16: COSSE; TSC_CON1_poignard
J19: CONN_01X05; Pin_Header_Straight_1x05_Pitch2.54mm
R1, R2, R3, R4, R5, R6: 1k; R_1206_HandSoldering
U1: MCP23008; SOIC-18
U2: 4081; SM_SO-14

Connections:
/C8051F38C/P0.0: R2.2, U1.2 (SDA); also elsewhere on the board
/C8051F38C/P0.1: R1.2, U1.1 (SCL); also elsewhere on the board
/C8051F38C/P0.2: J2.1; also elsewhere on the board
/C8051F38C/P0.3: J2.2; also elsewhere on the board
/C8051F38C/P0.4: J2.3; also elsewhere on the board
/C8051F38C/P0.5: J2.4; also elsewhere on the board
/C8051F38C/P0.6: U2.10; also elsewhere on the board
/C8051F38C/P0.7: U2.11; also elsewhere on the board
/C8051F38C/P2.0: J3.6, J19.4, R6.2, U2.8; also elsewhere on the board
/C8051F38C/P2.1: J3.3, J19.1, R3.2, U2.9; also elsewhere on the board
/C8051F38C/P2.2: J3.5, J19.3, R5.2, U2.12; also elsewhere on the board
/C8051F38C/P2.3: J3.4, J19.2, R4.2, U2.13; also elsewhere on the board
/C8051F38C/P2.4: J4.2; also elsewhere on the board
/C8051F38C/P2.5: J4.3; also elsewhere on the board
/C8051F38C/P2.6: J4.4; also elsewhere on the board
/C8051F38C/P2.7: J4.5; also elsewhere on the board
/C8051F38C/VCC(5V): J5.1, J15.1, R1.1, R2.1, U1.6 (~RESET), U1.18 (VCC); also elsewhere on the board
/DRV8825/VCC(12V): J5.2, J14.1; also elsewhere on the board
GND: J3.2, J4.1, J5.3, J13.1, J16.1, J19.5, U1.3 (A2), U1.4 (A1), U1.5 (A0), U1.9 (GND), U2.7 (VSS); also elsewhere on the board
unnamed: J1.1, U1.17 (GPB7)
unnamed: J1.2, U1.16 (GPB6)
unnamed: J1.3, U1.15 (GPB5)
unnamed: J1.4, U1.14 (GPB4)
unnamed: J1.5, U1.13 (GPB3)
unnamed: J1.6, U1.12 (GPB2)
unnamed: J1.7, U1.11 (GPB1)
unnamed: J1.8, U1.10 (GPB0)
VCC: J4.6, R3.1, R4.1, R5.1, R6.1, U2.14 (VDD); also elsewhere on the board

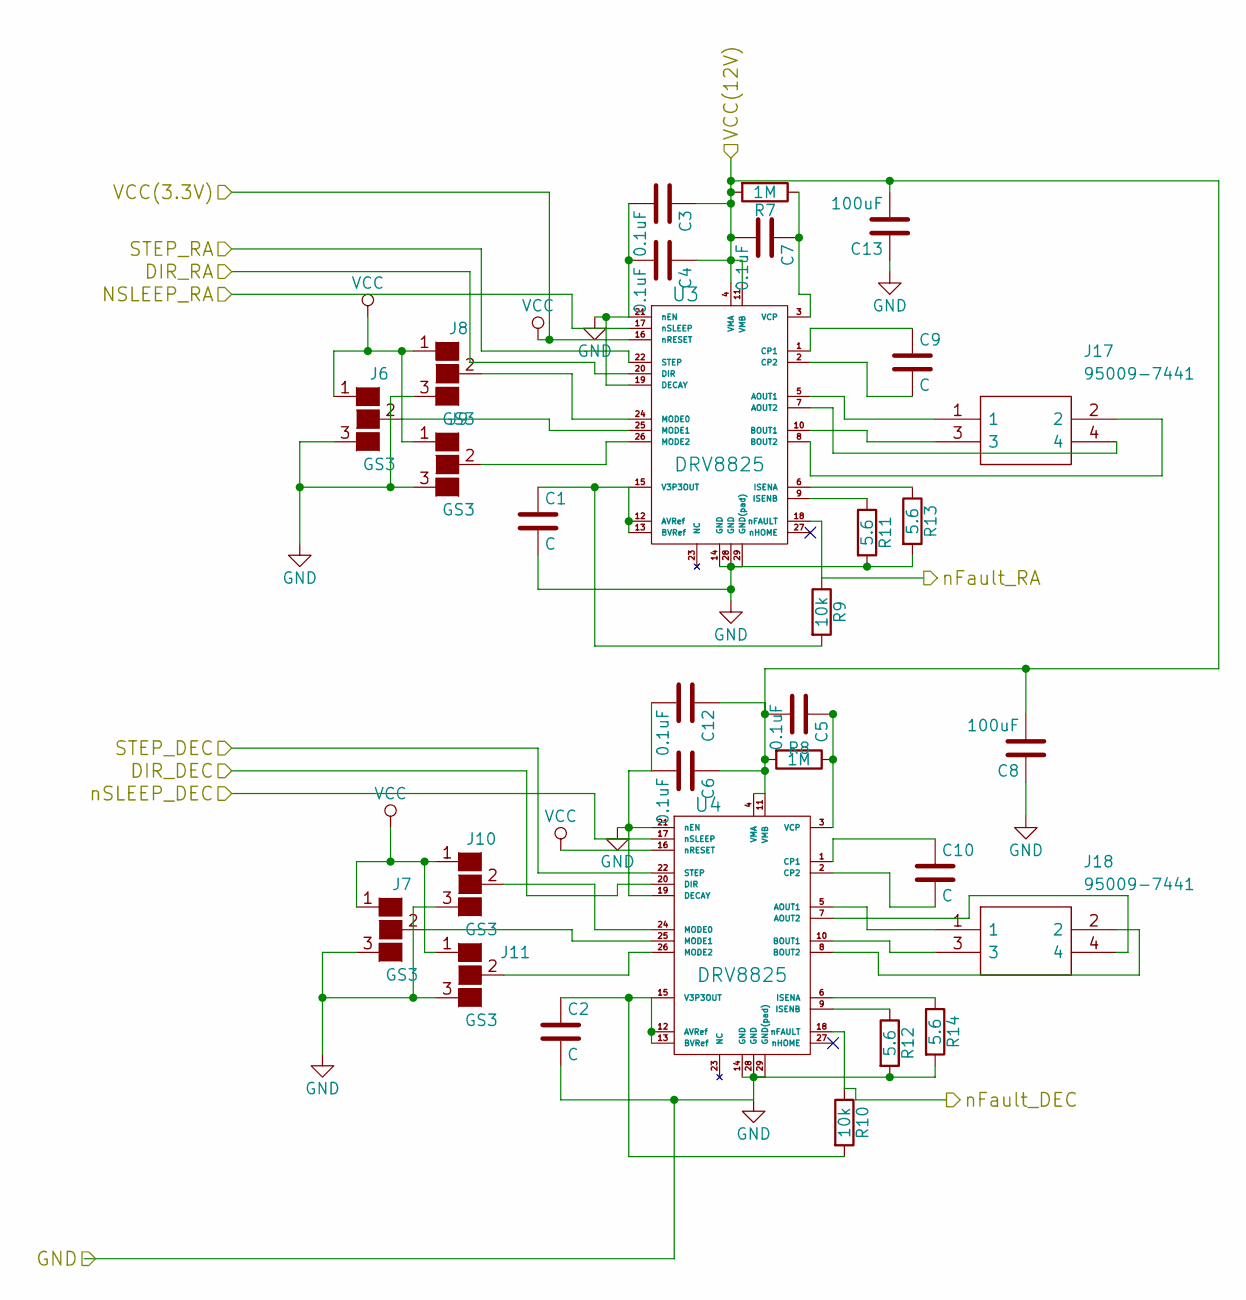
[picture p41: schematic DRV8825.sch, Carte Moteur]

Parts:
C1, C2, C9, C10: C; C_1206_HandSoldering
C3, C4, C5, C6, C7, C12: 0.1uF; C_1206_HandSoldering
C8, C13: 100uF; CP_Radial_D5.0mm_P2.00mm
J6, J7, J8, J9, J10, J11: GS3
J17, J18: 95009-7441; RJ11-95009-7441; Mouser Part Number 538-95009-7441
R7, R8: 1M; R_1206_HandSoldering
R9, R10: 10k; R_1206_HandSoldering
R11, R12, R13, R14: 5.6; R_1206_HandSoldering
U3, U4: DRV8825

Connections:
/C8051F38C/P1.1: R9.1, U3.18 (nFAULT); also elsewhere on the board
/C8051F38C/P1.3: U3.22 (STEP); also elsewhere on the board
/C8051F38C/P1.4: U4.17 (nSLEEP); also elsewhere on the board
/C8051F38C/P1.5: R10.1, U4.18 (nFAULT); also elsewhere on the board
/C8051F38C/P1.7: U4.22 (STEP); also elsewhere on the board
/DRV8825/DIR_DEC: U4.20 (DIR); also elsewhere on the board
/DRV8825/DIR_RA: U3.20 (DIR); also elsewhere on the board
/DRV8825/NSLEEP_RA: U3.17 (nSLEEP); also elsewhere on the board
/DRV8825/VCC(12V): C3.1, C4.1, C5.2, C6.1, C7.2, C8.2, C12.1, C13.2, R7.2, R8.2, U3.4 (VMA), U3.11 (VMB), U4.4 (VMA), U4.11 (VMB); also elsewhere on the board
GND: C1.2, C2.2, C3.2, C4.2, C6.2, C8.1, C12.2, C13.1, J6.3 (G3), J7.3 (G3), J8.3 (G3), J9.3 (G3), J10.3 (G3), J11.3 (G3), R11.2, R12.2, R13.2, R14.2, U3.14 (GND), U3.19 (DECAY), U3.21 (nEN), U3.28 (GND), U3.29 (GND(pad)), U4.14 (GND), U4.19 (DECAY), U4.21 (nEN), U4.28 (GND), U4.29 (GND(pad)); also elsewhere on the board
unnamed: C1.1, R9.2, U3.12 (AVRef), U3.13 (BVRef), U3.15 (V3P3OUT)
unnamed: C2.1, R10.2, U4.12 (AVRef), U4.13 (BVRef), U4.15 (V3P3OUT)
unnamed: C5.1, R8.1, U4.3 (VCP)
unnamed: C7.1, R7.1, U3.3 (VCP)
unnamed: C9.1, U3.1 (CP1)
unnamed: C9.2, U3.2 (CP2)
unnamed: C10.1, U4.1 (CP1)
unnamed: C10.2, U4.2 (CP2)
unnamed: J6.2 (G2), U3.25 (MODE1)
unnamed: J7.2 (G2), U4.25 (MODE1)
unnamed: J8.2 (G2), U3.24 (MODE0)
unnamed: J9.2 (G2), U3.26 (MODE2)
unnamed: J10.2 (G2), U4.24 (MODE0)
unnamed: J11.2 (G2), U4.26 (MODE2)
unnamed: J17.1, U3.5 (AOUT1)
unnamed: J17.2, U3.8 (BOUT2)
unnamed: J17.3, U3.10 (BOUT1)
unnamed: J17.4, U3.7 (AOUT2)
unnamed: J18.1, U4.5 (AOUT1)
unnamed: J18.2, U4.8 (BOUT2)
unnamed: J18.3, U4.10 (BOUT1)
unnamed: J18.4, U4.7 (AOUT2)
unnamed: R11.1, U3.9 (ISENB)
unnamed: R12.1, U4.9 (ISENB)
unnamed: R13.1, U3.6 (ISENA)
unnamed: R14.1, U4.6 (ISENA)
VCC: J6.1 (G1), J7.1 (G1), J8.1 (G1), J9.1 (G1), J10.1 (G1), J11.1 (G1), U3.16 (nRESET), U4.16 (nRESET); also elsewhere on the board

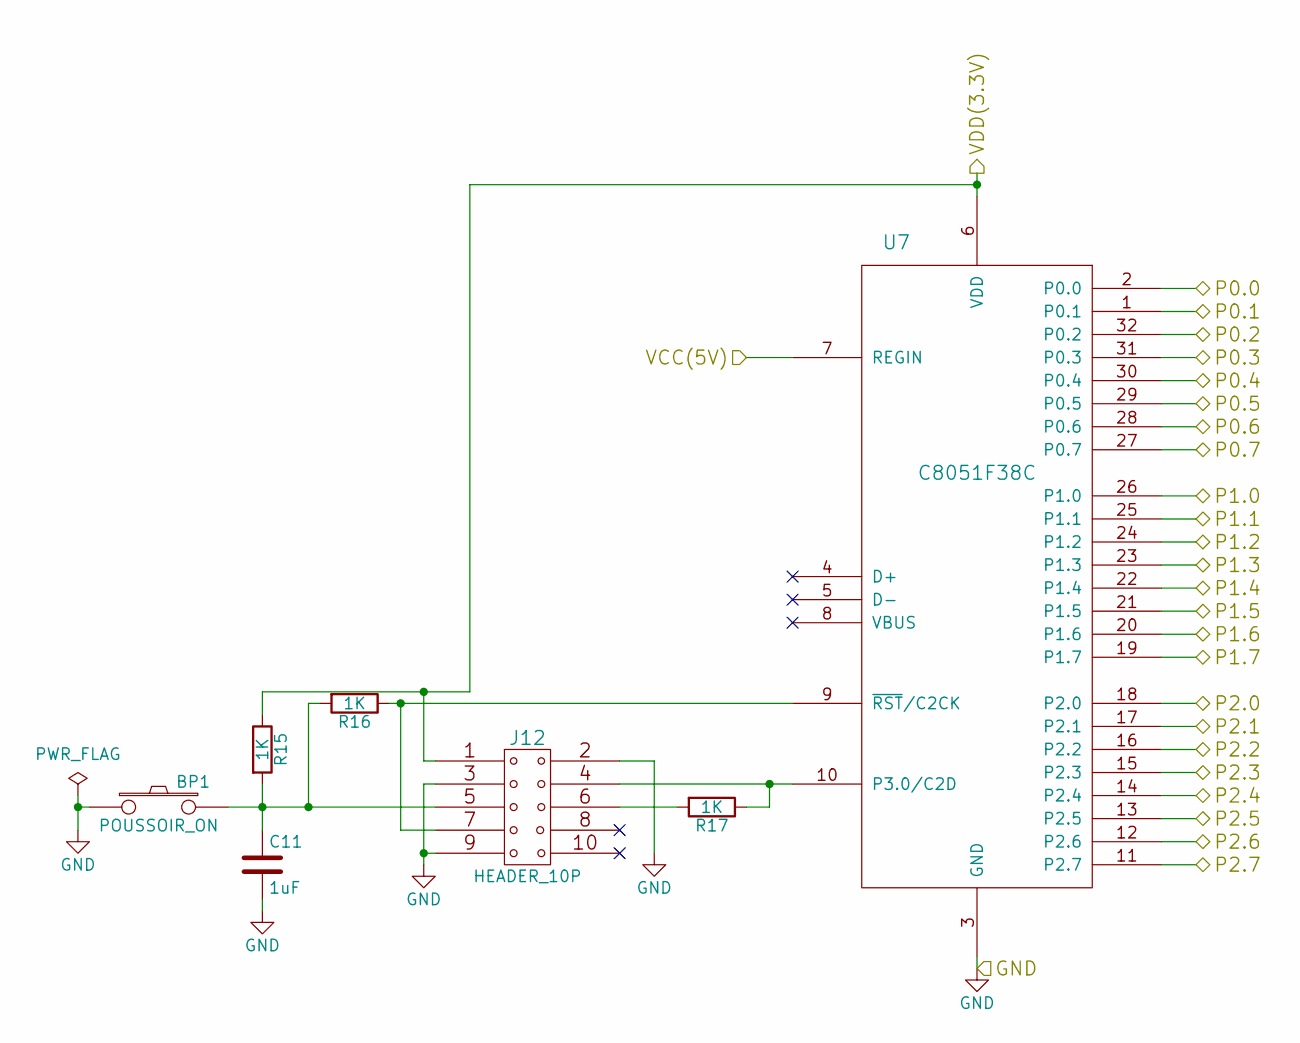
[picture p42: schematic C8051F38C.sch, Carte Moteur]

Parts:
BP1: POUSSOIR_ON; SW_PUSH_6mm
C11: 1uF; C_1206_HandSoldering
J12: HEADER_10P; JTAG
R15, R16, R17: 1K; R_1206_HandSoldering
U7: C8051F38C

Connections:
/C8051F38C/P0.0: U7.2 (P0.0); also elsewhere on the board
/C8051F38C/P0.1: U7.1 (P0.1); also elsewhere on the board
/C8051F38C/P0.2: U7.32 (P0.2); also elsewhere on the board
/C8051F38C/P0.3: U7.31 (P0.3); also elsewhere on the board
/C8051F38C/P0.4: U7.30 (P0.4); also elsewhere on the board
/C8051F38C/P0.5: U7.29 (P0.5); also elsewhere on the board
/C8051F38C/P0.6: U7.28 (P0.6); also elsewhere on the board
/C8051F38C/P0.7: U7.27 (P0.7); also elsewhere on the board
/C8051F38C/P1.1: U7.25 (P1.1); also elsewhere on the board
/C8051F38C/P1.3: U7.23 (P1.3); also elsewhere on the board
/C8051F38C/P1.4: U7.22 (P1.4); also elsewhere on the board
/C8051F38C/P1.5: U7.21 (P1.5); also elsewhere on the board
/C8051F38C/P1.7: U7.19 (P1.7); also elsewhere on the board
/C8051F38C/P2.0: U7.18 (P2.0); also elsewhere on the board
/C8051F38C/P2.1: U7.17 (P2.1); also elsewhere on the board
/C8051F38C/P2.2: U7.16 (P2.2); also elsewhere on the board
/C8051F38C/P2.3: U7.15 (P2.3); also elsewhere on the board
/C8051F38C/P2.4: U7.14 (P2.4); also elsewhere on the board
/C8051F38C/P2.5: U7.13 (P2.5); also elsewhere on the board
/C8051F38C/P2.6: U7.12 (P2.6); also elsewhere on the board
/C8051F38C/P2.7: U7.11 (P2.7); also elsewhere on the board
/C8051F38C/VCC(5V): U7.7 (REGIN); also elsewhere on the board
/DRV8825/DIR_DEC: U7.20 (P1.6); also elsewhere on the board
/DRV8825/DIR_RA: U7.24 (P1.2); also elsewhere on the board
/DRV8825/NSLEEP_RA: U7.26 (P1.0); also elsewhere on the board
GND: BP1.1, C11.2, J12.2, J12.3, J12.9, U7.3 (GND); also elsewhere on the board
unnamed: BP1.2, C11.1, J12.5, R15.2, R16.2
unnamed: J12.4, R17.1, U7.10 (P3.0/C2D)
unnamed: J12.6, R17.2
unnamed: J12.7, R16.1, U7.9 (~RST~/C2CK)
VCC: J12.1, R15.1, U7.6 (VDD); also elsewhere on the board

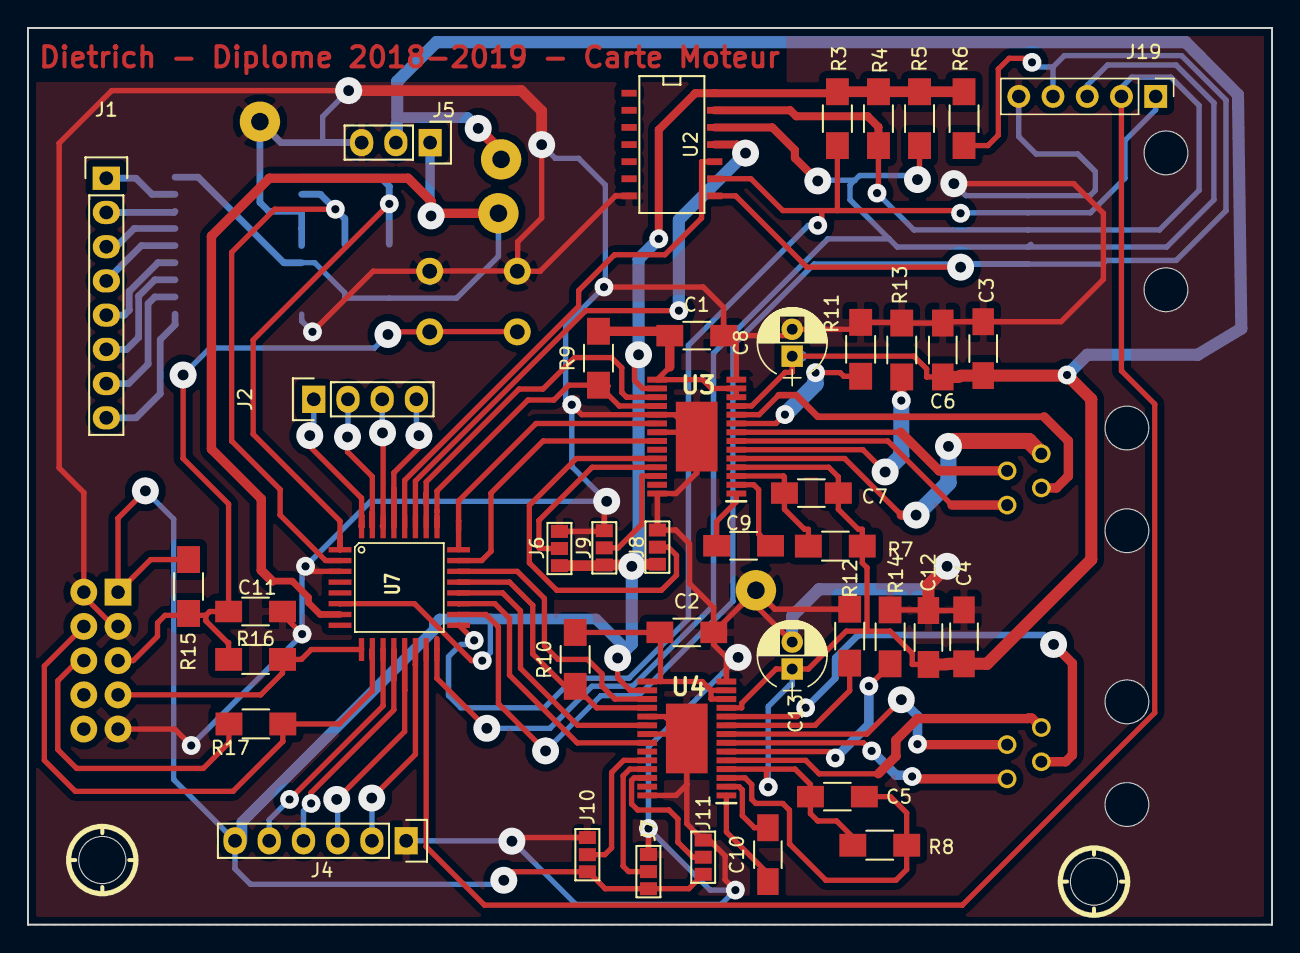
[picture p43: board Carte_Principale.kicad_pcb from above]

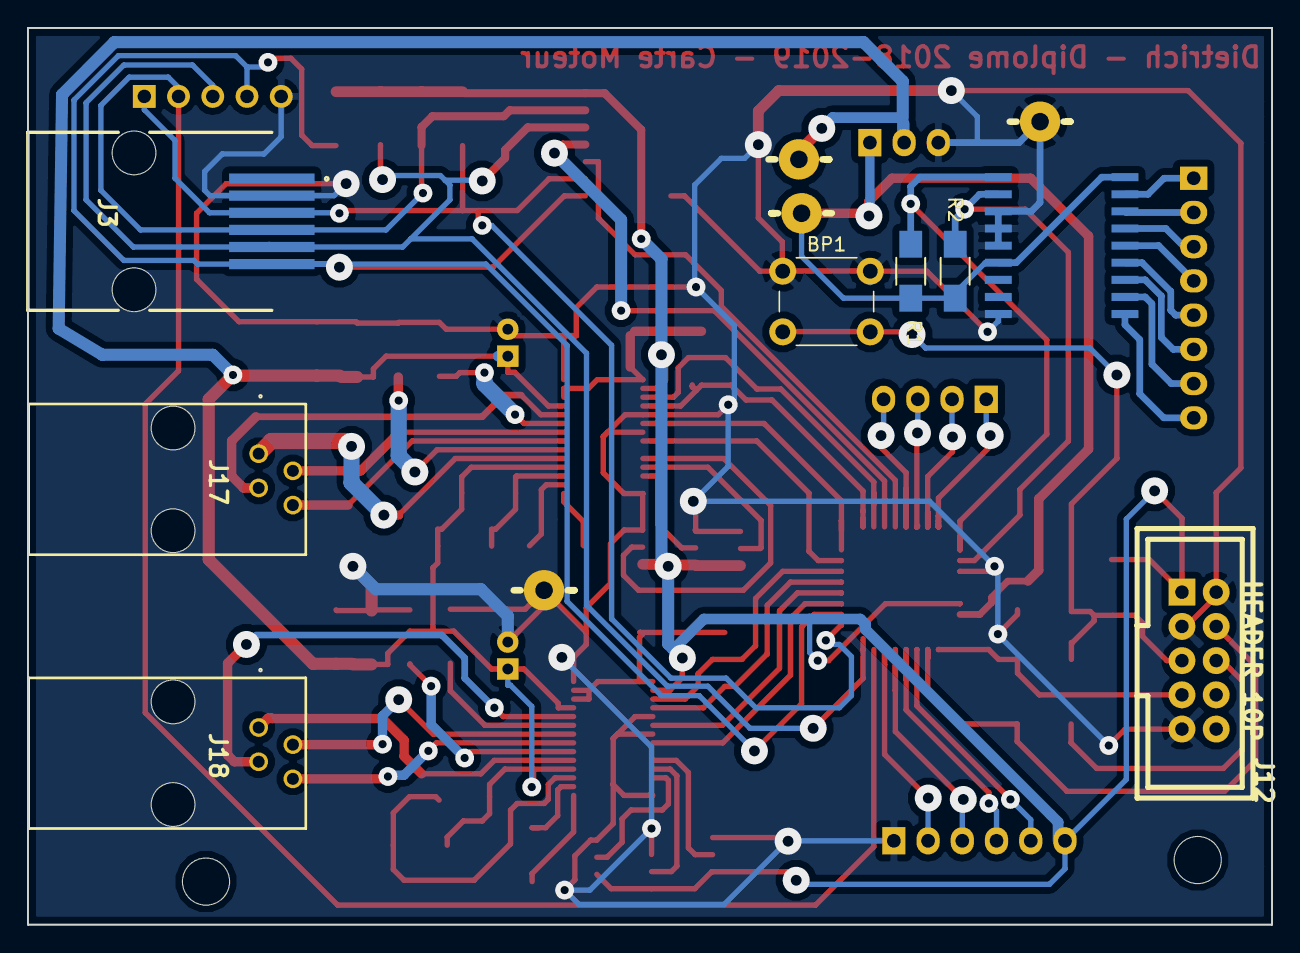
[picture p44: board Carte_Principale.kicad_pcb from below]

Board: 2 copper layers, 92.3 x 66.5 mm, 57 parts (12 on the bottom side), 66 nets.

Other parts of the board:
TROU_3.5, TROU_3.5#2: Val**; TROU_3.5

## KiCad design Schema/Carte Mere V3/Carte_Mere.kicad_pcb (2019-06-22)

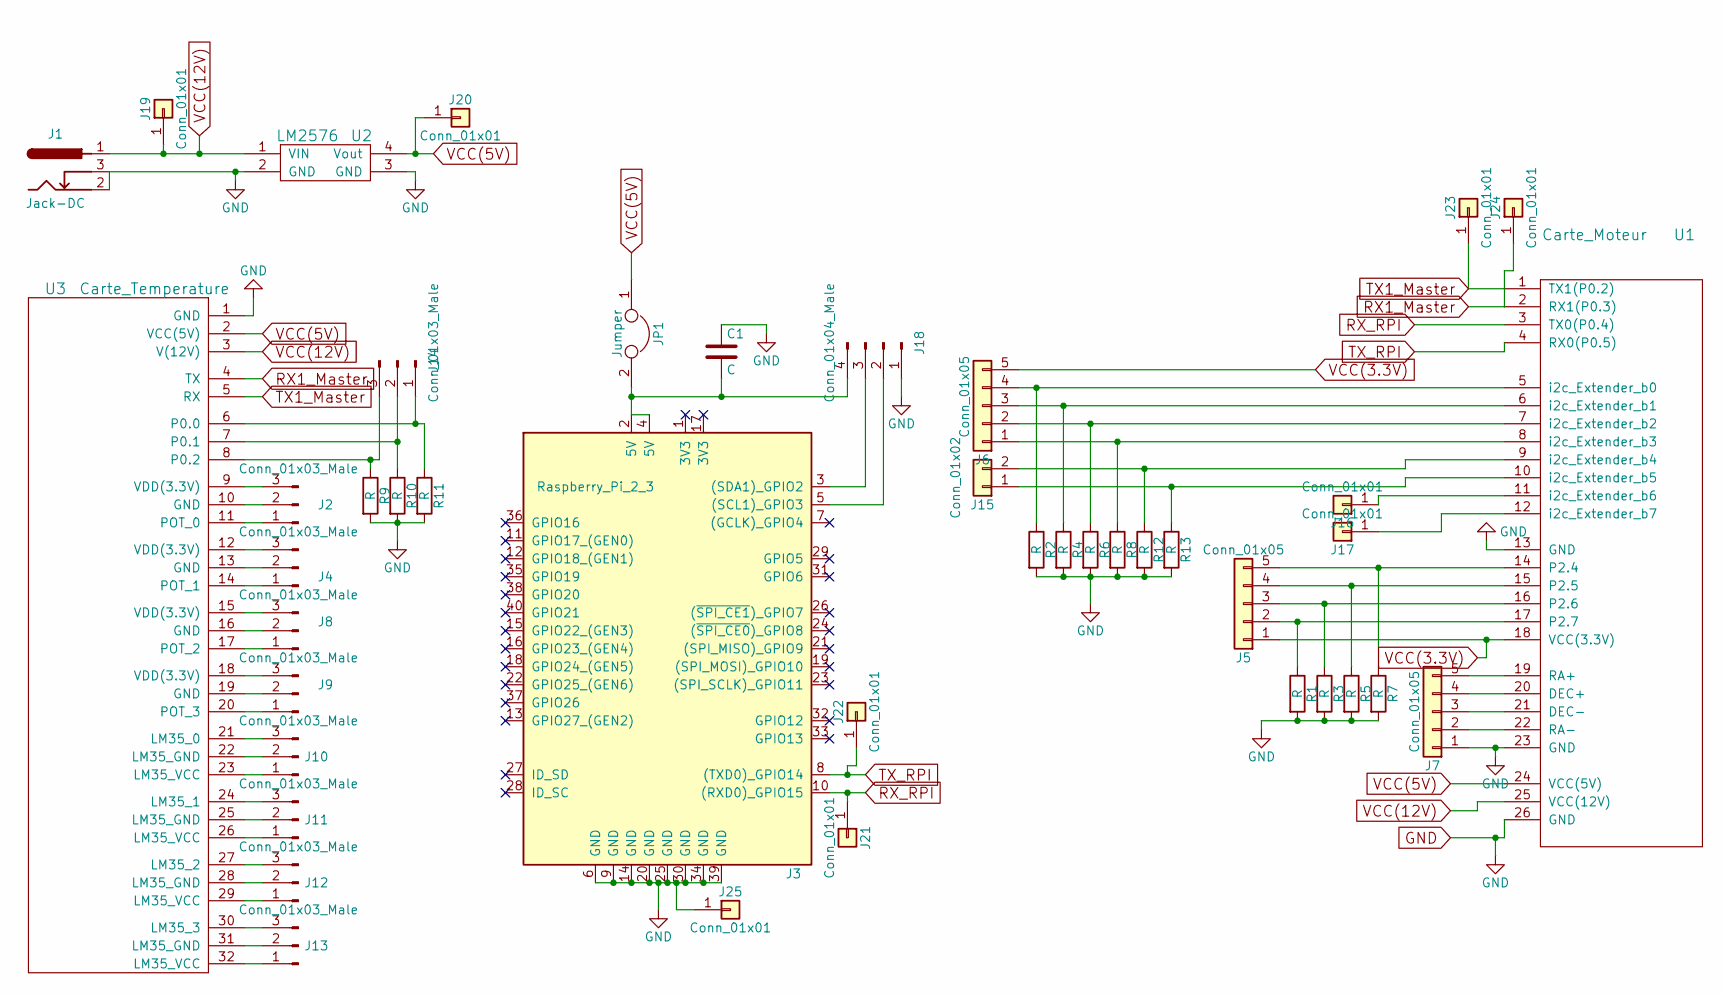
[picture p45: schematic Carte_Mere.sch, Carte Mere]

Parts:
C1: C; CP_Radial_D5.0mm_P2.00mm
J1: Jack-DC; JACK_ALIM
J2, J4, J8, J9, J10, J11, J12, J13, J14: Conn_01x03_Male; Pin_Header_Straight_1x03_Pitch2.54mm
J3: Raspberry_Pi_2_3; RaspberryPI3_V2
J5, J6, J7: Conn_01x05; Pin_Header_Straight_1x05_Pitch2.54mm
J15: Conn_01x02; Pin_alimentation
J16, J17, J19, J20, J21, J22, J23, J24, J25: Conn_01x01; TSC_CON1_poignard
J18: Conn_01x04_Male; Pin_Header_Straight_1x04_Pitch2.54mm
JP1: Jumper; Pin_alimentation
R1, R2, R3, R4, R5, R6, R7, R8, R9, R10, R11, R12, R13: R; R_1206_HandSoldering
U1: Carte_Moteur; Carte_Moteur_V2
U2: LM2576; Alimentation_V2
U3: Carte_Temperature

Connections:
GND: C1.1, J1.2, J1.3, J3.6 (GND), J3.9 (GND), J3.14 (GND), J3.20 (GND), J3.25 (GND), J3.30 (GND), J3.34 (GND), J3.39 (GND), J7.1, J18.1, J25.1, R1.2, R2.2, R3.2, R4.2, R5.2, R6.2, R7.2, R8.2, R9.2, R10.2, R11.2, R12.2, R13.2, U1.13 (GND), U1.23 (GND), U1.26 (GND), U2.2 (GND), U2.3 (GND), U3.1 (GND)
unnamed: C1.2, J3.2 (5V), J3.4 (5V), J18.4, JP1.2
unnamed: J2.1, U3.11 (POT_0)
unnamed: J2.2, U3.10 (GND)
unnamed: J2.3, U3.9 (VDD(3.3V))
unnamed: J4.1, U3.14 (POT_1)
unnamed: J4.2, U3.13 (GND)
unnamed: J4.3, U3.12 (VDD(3.3V))
unnamed: J5.2, R1.1, U1.17 (P2.7)
unnamed: J5.3, R3.1, U1.16 (P2.6)
unnamed: J5.4, R5.1, U1.15 (P2.5)
unnamed: J5.5, R7.1, U1.14 (P2.4)
unnamed: J6.1, R8.1, U1.8 (i2c_Extender_b3)
unnamed: J6.2, R6.1, U1.7 (i2c_Extender_b2)
unnamed: J6.3, R4.1, U1.6 (i2c_Extender_b1)
unnamed: J6.4, R2.1, U1.5 (i2c_Extender_b0)
unnamed: J7.2, U1.22 (RA-)
unnamed: J7.3, U1.21 (DEC-)
unnamed: J7.4, U1.20 (DEC+)
unnamed: J7.5, U1.19 (RA+)
unnamed: J8.1, U3.17 (POT_2)
unnamed: J8.2, U3.16 (GND)
unnamed: J8.3, U3.15 (VDD(3.3V))
unnamed: J9.1, U3.20 (POT_3)
unnamed: J9.2, U3.19 (GND)
unnamed: J9.3, U3.18 (VDD(3.3V))
unnamed: J10.1, U3.23 (LM35_VCC)
unnamed: J10.2, U3.22 (LM35_GND)
unnamed: J10.3, U3.21 (LM35_0)
unnamed: J11.1, U3.26 (LM35_VCC)
unnamed: J11.2, U3.25 (LM35_GND)
unnamed: J11.3, U3.24 (LM35_1)
unnamed: J12.1, U3.29 (LM35_VCC)
unnamed: J12.2, U3.28 (LM35_GND)
unnamed: J12.3, U3.27 (LM35_2)
unnamed: J13.1, U3.32 (LM35_VCC)
unnamed: J13.2, U3.31 (LM35_GND)
unnamed: J13.3, U3.30 (LM35_3)
unnamed: J14.1, R11.1, U3.6 (P0.0)
unnamed: J14.2, R10.1, U3.7 (P0.1)
unnamed: J14.3, R9.1, U3.8 (P0.2)
unnamed: J15.1, R13.1, U1.10 (i2c_Extender_b5)
unnamed: J15.2, R12.1, U1.9 (i2c_Extender_b4)
unnamed: J16.1, U1.11 (i2c_Extender_b6)
unnamed: J17.1, U1.12 (i2c_Extender_b7)
unnamed: J3.5 ((SCL1)_GPIO3), J18.2
unnamed: J3.3 ((SDA1)_GPIO2), J18.3
RX1_Master: J24.1, U1.2 (RX1(P0.3)), U3.4 (TX)
RX_RPI: J3.10 ((RXD0)_GPIO15), J21.1, U1.3 (TX0(P0.4))
TX1_Master: J23.1, U1.1 (TX1(P0.2)), U3.5 (RX)
TX_RPI: J3.8 ((TXD0)_GPIO14), J22.1, U1.4 (RX0(P0.5))
VCC(3.3V): J5.1, J6.5, U1.18 (VCC(3.3V))
VCC(5V): J20.1, JP1.1, U1.24 (VCC(5V)), U2.4 (Vout), U3.2 (VCC(5V))
VCC(12V): J1.1, J19.1, U1.25 (VCC(12V)), U2.1 (VIN), U3.3 (V(12V))

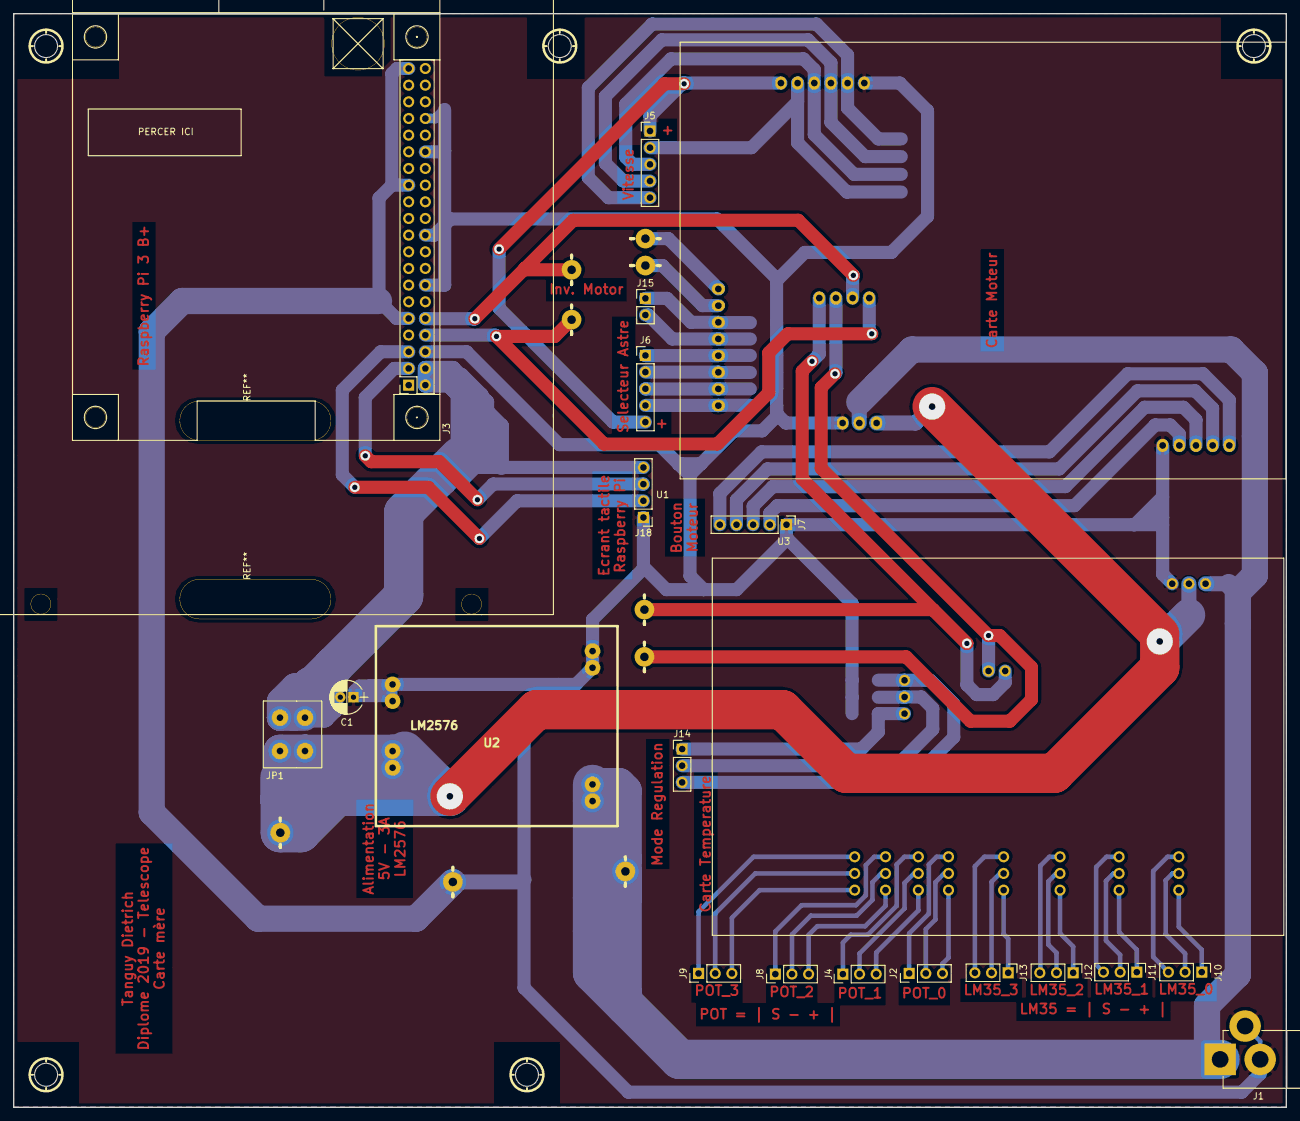
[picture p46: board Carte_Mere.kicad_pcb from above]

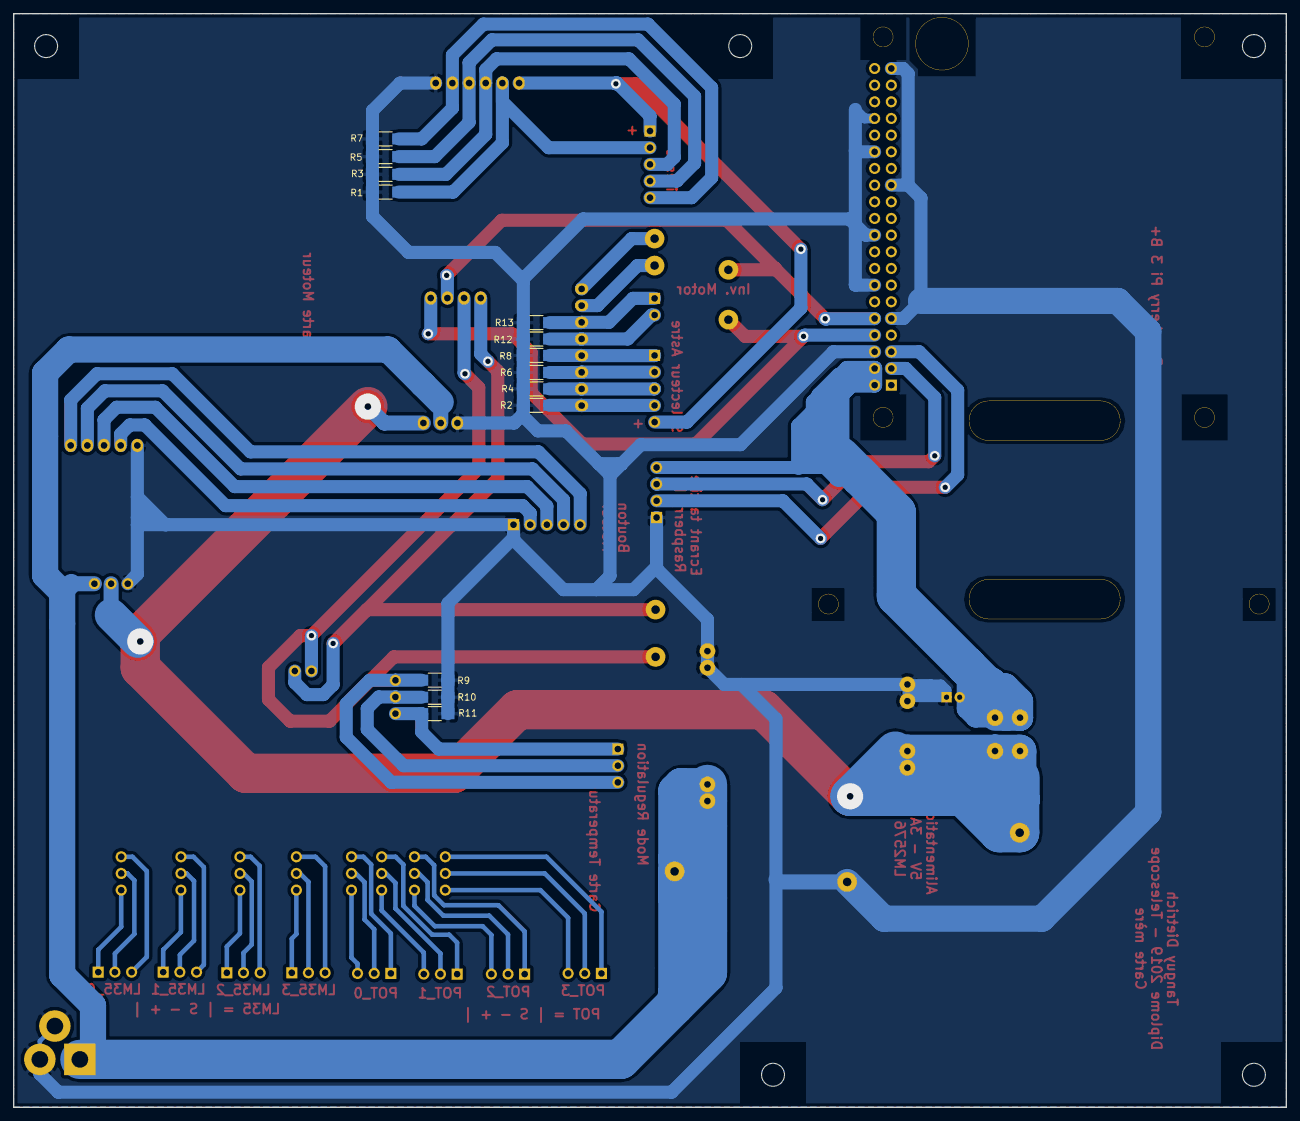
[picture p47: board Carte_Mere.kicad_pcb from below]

Board: 2 copper layers, 194.0 x 166.7 mm, 48 parts (15 on the bottom side), 54 nets.

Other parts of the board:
TROU_3.5, TROU_3.5#2, TROU_3.5#3, TROU_3.5#4, TROU_3.5#5: Val**; TROU_3.5

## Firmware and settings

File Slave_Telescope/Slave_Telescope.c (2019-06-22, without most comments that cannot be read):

/*===========================================================================*=
	Slave_telescope - Tanguy Dietrich
  =============================================================================
   Descriptif: Permet de reguler la temperature des miroir ou des lentille
   			   d'un telescope en utilisant la temperature du point de rose
   			   ou des potentiometre
   
=*===========================================================================*/

#include <reg51f380.h>     // registres 51f38C
#include "SmBus0.h"
#include "PID.h"
#include "Delay48M.h"
#include "math.h"

#define LOADVALUE_T0 15536
#define LOADVALUE_BAUD 247

// ==== FONCTIONS PROTOTYPES===================================================
void ClockInit ();
void PortInit ();          // init. config des ports
void SMBus_Init (void);
void Timer3_Init (void);
void Timer2_Init (void);
void Uart0Init();
void SMB_Write (void);
void SMB_Read (void);
void PCA_Init();
void decodeUart0();
void TimerInit();
void ADCInit();
void configEeh210(unsigned char mode);
long convertToTemp_i2c(unsigned int value);
unsigned int convertToHumi(unsigned int value);
long getTempAmbiante();
unsigned int GetHumidite();
void actu_Pca0_Pid(int tempCapt,int consigne);
void actu_Pca1_Pid(int tempCapt,int consigne);
void actu_Pca2_Pid(int tempCapt,int consigne);
void actu_Pca3_Pid(int tempCapt,int consigne);
int convertLm35ToTemp(unsigned int adc_pos,unsigned int adc_neg);
void reset_i2c();
int calculRose(float t_ambiante, float humidite);
unsigned char ConvertToPca(unsigned int adc);
void ActuAvgMesure(unsigned int tabMesure[12][NMESURE], unsigned int tabSortie[]);
sbit SDA = P0^6;
sbit SCL= P0^7;
// ==== MAIN ==================================================================

//SMBus0
unsigned char gSMBNumBytesToWR = 2; // Number of bytes to write
                                    // Master -> Slave
unsigned char gSMBNumBytesToRD = 3; // Number of bytes to read
                                    // Master <- Slave

// Global holder for SMBus data
// All receive data is written here
xdata unsigned char gSMBDataIN[NUM_BYTES_MAX_RD];

// Global holder for SMBus data.
// All transmit data is read from here
xdata unsigned char gSMBDataOUT[NUM_BYTES_MAX_WR];

unsigned char gTarget;                  // gTarget SMBus slave address

bit SMB_BUSY;                          // Software flag to indicate when the
                                       // SMB_Read() or SMB_Write() functions
                                       // have claimed the SMBus

bit SMB_RW;                            // Software flag to indicate the
                                       // direction of the current transfer

xdata unsigned long NUM_ERRORS;              // Counter for the number of errors.



//Uart
xdata unsigned char gUart0Tx[15]="";
xdata unsigned char gUart0Rx[15];
unsigned char gUart0NbrByteTx=0;
unsigned char gUart0NbrByteRx=0;
bit gUart0FlagReceive;

//Mesure ADC
xdata unsigned int gMesure[12][NMESURE];
xdata unsigned int gMesureAvg[12];
bit gFlagMesureAvg=0;

bit gFlagActuI2c=0;
long gTempAmbiante=0;
unsigned int gHumidite=0;
unsigned char gModeRegulation=MODE_UART;
bit gFlagPot=0;
void main () 
{
   //unsigned char i=0;
   //unsigned char temp_pwm=0;
   int tempSensor;
   int temp_rose=0;
   PCA0MD &= ~0x40;     // WDTE = 0 (disable watchdog timer)
   ClockInit ();
   PortInit ();         // init. config des ports
   Timer3_Init();                      // Configure Timer3 for use with SMBus
                                       // low timeout detect
   Timer2_Init();
   SMBus_Init ();                      // Configure and enable SMBus
   PCA_Init();
   TimerInit();
   Uart0Init();
   ADCInit();
   
   EA=1;//Autorise toutes les interruption
   IE|=0x90;
   EIE1 |= 0x09;
   TR1=1;
   TR0=1;
	SDA=1;
   reset_i2c();
   configEeh210(0);
   gHumidite=GetHumidite();
   gTempAmbiante=getTempAmbiante();
   while (1)
   {
      gModeRegulation=P0&0x07;
      if(gUart0FlagReceive)
      {
         gUart0FlagReceive=0;
         decodeUart0();
      }
      
      if(gFlagMesureAvg)
      {
         gFlagMesureAvg=0;
         ActuAvgMesure(gMesure,gMesureAvg);
         if(gModeRegulation==MODE_PID)
         {
            tempSensor=convertLm35ToTemp(gMesureAvg[LM35_0_POS],gMesureAvg[LM35_0_NEG]);
            actu_Pca0_Pid(tempSensor,temp_rose);
            
            tempSensor=convertLm35ToTemp(gMesureAvg[LM35_1_POS],gMesureAvg[LM35_1_NEG]);
            actu_Pca1_Pid(tempSensor,temp_rose);
            
            tempSensor=convertLm35ToTemp(gMesureAvg[LM35_2_POS],gMesureAvg[LM35_2_NEG]);
            actu_Pca2_Pid(tempSensor,temp_rose);
            
            tempSensor=convertLm35ToTemp(gMesureAvg[LM35_3_POS],gMesureAvg[LM35_3_NEG]);
            actu_Pca3_Pid(tempSensor,temp_rose);
         }
      }
      
      if(gFlagPot)
      {
         gFlagPot=0;
         if(gModeRegulation==MODE_POT)
         {
            PCA0CPH0=ConvertToPca(gMesure[POT_0][0]);
            PCA0CPH1=ConvertToPca(gMesure[POT_1][0]);
            PCA0CPH2=ConvertToPca(gMesure[POT_2][0]);
            PCA0CPH3=ConvertToPca(gMesure[POT_3][0]);
         }
      }
      
      if(gFlagActuI2c)
      {
         gHumidite=GetHumidite();
         gTempAmbiante=getTempAmbiante();
         temp_rose=calculRose(gTempAmbiante, gHumidite);
         temp_rose+=CORRECTION_TEMPERATURE;
         //temp_rose=DEMO_CONSIGNE;
         gFlagActuI2c=0;
         //temp_rose=calculRose(300, 60);
      }
   } // End while (1)
} // main =====================================================================

/*---------------------------------------------------------------------------*-
timer0()
-----------------------------------------------------------------------------
Descriptif: Fonction d'interruption Timer0 vecteur 1
          Temporisation de 50milli
          Mode : 16bit
Entree    : --
Sortie    : --
-*---------------------------------------------------------------------------*/
void timer0() interrupt 1
{
   static unsigned char cpt_i2c=0;
   static unsigned char cpt_adc=0;
   TR0=0;
   TH0=LOADVALUE_T0/256;//Charge la valeur dans le registre MSB du timer 0
   TL0=LOADVALUE_T0%256;//Charge la valeur dans le registre LSB du timer 0
   //TR0=1;
   if(cpt_adc>=DELAI_MESURE)
   {
      cpt_adc=0;
      AD0BUSY=1;
   }
   cpt_adc++;
   if(cpt_i2c>=20)
   {
      cpt_i2c=0;
      gFlagActuI2c=1;
   }
   cpt_i2c++;
   TR0=1;
}

/*---------------------------------------------------------------------------*-
ADCComplete()
-----------------------------------------------------------------------------
Descriptif: fonction d'interruption de fin de conversion de l'ADC vecteur 10
Pin + : P1.1
Pin - : GND
Aligner a Droite
Conversion sur : AD0BUSY=1;
Clock SAR : 2000000
Entree    : --
Sortie    : --
-*---------------------------------------------------------------------------*/
void ADCComplete() interrupt 10
{
   unsigned char i=0;
   static unsigned char cptMesure=0;
   gMesure[AMX0P][cptMesure]=ADC0L+(ADC0H<<8);
   if(AMX0P<=0x0A)
   {
      AMX0P++;//change le canal de l'ADC a P2.3
      for(i=0;i<25;i++)//Attend que les condensateur se decharge
      {
         
      }
      AD0BUSY=1;//lance une conversion
   }
   else
   {
      AMX0P=0x00;//remet le canal P2.0
      //MovingAvg(gMesure,gAvgMesure);
      cptMesure++;
      gFlagPot=1;
      if(cptMesure==NMESURE)
      {
         gFlagMesureAvg=1;//Mets le flag a 1 pour signifier au main d'actualiser
         cptMesure=0;
      }
   }
	AD0INT=0;
}

/*---------------------------------------------------------------------------*-
uart0()
-----------------------------------------------------------------------------
Descriptif: Fonction d'interruption de l'uart0 vecteur 4
Entree    : --
Sortie    : --
-*---------------------------------------------------------------------------*/
void uart0() interrupt 4
{
   if(TI0)
   {
      TI0=0;
      if(gUart0Tx[gUart0NbrByteTx]!=0)
      {
         SBUF0=gUart0Tx[gUart0NbrByteTx];
         gUart0NbrByteTx++;
      }
      else
      {
         gUart0NbrByteTx=0;
      }
   }
   
   if(RI0)
   {
      RI0=0;
      gUart0Rx[gUart0NbrByteRx]=SBUF0;
      if(gUart0Rx[gUart0NbrByteRx]=='#')
       {
          gUart0FlagReceive=1;
          gUart0NbrByteRx=0;
       }
       else
       {
          gUart0NbrByteRx=(gUart0NbrByteRx+1)%20;
       }
   }
}

/*---------------------------------------------------------------------------*-
   ActuAvgMesure ()
  -----------------------------------------------------------------------------
   Descriptif: Calcul la moyenne de mesure effectuer par l'ADC
   Entrée    : 
               - unsigned int tabMesure[12][NMESURE] - tableau de mesure
               - unsigend int tabSortie[] - tableau de sortie pour les moyenne
   Sortie    : --
-*---------------------------------------------------------------------------*/
void ActuAvgMesure(unsigned int tabMesure[12][NMESURE], unsigned int tabSortie[])
{
   unsigned char canal=0;
   unsigned char nMesure=0;
   unsigned long somme;
   for(canal=0;canal<12;canal++)
   {
      somme=0;
      for(nMesure=0;nMesure<NMESURE;nMesure++)
      {
         somme+=tabMesure[canal][nMesure];
      }
      tabSortie[canal]=somme/NMESURE;
   }
}

/*---------------------------------------------------------------------------*-
   ConvertToPca ()
  -----------------------------------------------------------------------------
   Descriptif: Convertie une valeur entre 0 et 1023, de 0 a 255
   Entrée    : unsigend int adc (0 ... 1023)
   Sortie    : unsigend char (0 ... 255)
-*---------------------------------------------------------------------------*/
unsigned char ConvertToPca(unsigned int adc)
{
   return 255-((unsigned long)adc*255)/1023;
}

/*---------------------------------------------------------------------------*-
   calculRose ()
  -----------------------------------------------------------------------------
   Descriptif: 
   Entrée    : 
               - float t_ambiante
               - float humidite
   Sortie    : int (-32767 ... +32767) la temperature du point de rosé
               Ex : -2767 --> -27.67[C]
-*---------------------------------------------------------------------------*/
int calculRose(float t_ambiante, float humidite)
{
   float tRose=0;
   tRose=pow(((float)humidite/100),0.125);
   tRose=tRose*(112+(9*t_ambiante)/1000);
   tRose+=((t_ambiante)/1000)-112;
   return tRose*10;
}

/*---------------------------------------------------------------------------*-
   convertLm35ToTemp ()
  -----------------------------------------------------------------------------
   Descriptif: 
   Entrée    : --
   Sortie    : --
-*---------------------------------------------------------------------------*/
int convertLm35ToTemp(unsigned int adc_pos,unsigned int adc_neg)
{
   int temp=0;
   temp=adc_pos-adc_neg;
   temp=((long)temp*REF_ADC)/100;
   return temp;
}

/*---------------------------------------------------------------------------*-
   actu_Pca0_Pid ()
  -----------------------------------------------------------------------------
   Descriptif: calul le pwm a appliquer sur la resistance en fonction du PID
   Entrée    : 
               - int tempCapt
               - int consigne
   Sortie    : --
-*---------------------------------------------------------------------------*/
void actu_Pca0_Pid(int tempCapt,int consigne)
{
   static int pwm1=0;
   static unsigned char old_error=0;
   int error=0;
   if(tempCapt<consigne)
   {
      error=consigne-tempCapt;
      pwm1=255-((int)error*KP)+((old_error-error)*KD);
      //pwm1=0;//mode tout ou rien
   }
   else
   {
      pwm1=255;//0%
      error=0;
   }
   old_error=error;
   if(pwm1<=0)
   {
      PCA0CPM0|=0x40;//reactive le pca0 si il a ete desactiver
      PCA0CPH0=0;
   }
   else if(pwm1>=255)
   {
      PCA0CPH0=255;
      PCA0CPM0&=~0x40;//Clear ecom0 afin d'obtenir 0%
   }
   else
   {
      PCA0CPH0=pwm1;
   }
}

/*---------------------------------------------------------------------------*-
   actu_Pca1_Pid ()
  -----------------------------------------------------------------------------
   Descriptif: calul le pwm a appliquer sur la resistance en fonction du PID
   Entrée    : 
               - int tempCapt
               - int consigne
   Sortie    : --
-*---------------------------------------------------------------------------*/
void actu_Pca1_Pid(int tempCapt,int consigne)
{
   static int pwm1=0;
   static unsigned char old_error=0;
   int error=0;
   if(tempCapt<consigne)
   {
      error=consigne-tempCapt;
      pwm1=255-((int)error*KP)+((old_error-error)*KD);
      //pwm1=0;//mode tout ou rien
   }
   else
   {
      pwm1=255;//0%
      error=0;
   }
   old_error=error;
   if(pwm1<=0)
   {
      PCA0CPM1|=0x40;//reactive la pca0 si il a ete desactiver
      PCA0CPH1=0;
   }
   else if(pwm1>=255)
   {
      PCA0CPH1=255;
      PCA0CPM1&=~0x40;//Clear ecom0 afin d'obtenir 0%
   }
   else
   {
      PCA0CPH1=pwm1;
   }
}

/*---------------------------------------------------------------------------*-
   actu_Pca2_Pid ()
  -----------------------------------------------------------------------------
   Descriptif: calul le pwm a appliquer sur la resistance en fonction du PID
   Entrée    : 
               - int tempCapt
               - int consigne
   Sortie    : --
-*---------------------------------------------------------------------------*/
void actu_Pca2_Pid(int tempCapt,int consigne)
{
   static int pwm1=0;
   static unsigned char old_error=0;
   int error=0;
   if(tempCapt<consigne)
   {
      error=consigne-tempCapt;
      pwm1=255-((int)error*KP)+((old_error-error)*KD);
      //pwm1=0;//mode tout ou rien
   }
   else
   {
      pwm1=255;//0%
      error=0;
   }
   old_error=error;
   if(pwm1<=0)
   {
      PCA0CPM2|=0x40;//reactive la pca0 si il a ete desactiver
      PCA0CPH2=0;
   }
   else if(pwm1>=255)
   {
      PCA0CPH2=255;
      PCA0CPM2&=~0x40;//Clear ecom0 afin d'obtenir 0%
   }
   else
   {
      PCA0CPH2=pwm1;
   }
}

/*---------------------------------------------------------------------------*-
   actu_Pca3_Pid ()
  -----------------------------------------------------------------------------
   Descriptif: calul le pwm a appliquer sur la resistance en fonction du PID
   Entrée    : 
               - int tempCapt
               - int consigne
   Sortie    : --
-*---------------------------------------------------------------------------*/
void actu_Pca3_Pid(int tempCapt,int consigne)
{
   static int pwm1=0;
   static unsigned char old_error=0;
   int error=0;
   if(tempCapt<consigne)
   {
      error=consigne-tempCapt;
      pwm1=255-((int)error*KP)+((old_error-error)*KD);
      //pwm1=0;//mode tout ou rien
   }
   else
   {
      pwm1=255;//0%
      error=0;
   }
   old_error=error;
   if(pwm1<=0)
   {
      PCA0CPM3|=0x40;//reactive la pca0 si il a ete desactiver
      PCA0CPH3=0;
   }
   else if(pwm1>=255)
   {
      PCA0CPH3=255;
      PCA0CPM3&=~0x40;//Clear ecom0 afin d'obtenir 0%
   }
   else
   {
      PCA0CPH3=pwm1;
   }
}

/*---------------------------------------------------------------------------*-
reset_i2c()
-----------------------------------------------------------------------------
Descriptif: Verifie si le bus I2C est bloquer, et effectue un reset du bus
Entree    : --
Sortie    : --
-*---------------------------------------------------------------------------*/
void reset_i2c()
{
   unsigned char i=0;
	if(!SDA)
	{
		P0SKIP    = 0xCF;
		XBR0      = 0x01;
		// If slave is holding SDA low because of an improper SMBus reset or error
		while(!SDA)
		{
			// Provide clock pulses to allow the slave to advance out
			// of its current state. This will allow it to release SDA.
			SCL = 0;                         // Drive the clock low
			for(i = 0; i < 100; i++);        // Hold the clock low
			SCL = 1;                         // Release the clock
			for(i = 0; i < 100; i++);        // Hold the clock low
		}
		P0SKIP    = 0x0F;
		XBR0      = 0x05;
	}
}

/*---------------------------------------------------------------------------*-
   getTempAmbiante ()
  -----------------------------------------------------------------------------
   Descriptif: demande la temperature au capteur EEH210
   Entrée    : --
   Sortie    : long
-*---------------------------------------------------------------------------*/
long getTempAmbiante()
{
   while(SMB_BUSY);
			gTarget = 0x80;//0x81    (0x40 7 bit + 1 bit = 0x81 1 == read 
         gSMBDataOUT[0]  = 0xF3;//E3 = Hold master / F3 = no hold master
         gSMBNumBytesToWR = 1;
         SMB_Write();  // Initiate SMBus write
		//TEST=~TEST;
			while(SMB_BUSY);
		Delay_1ms(20);//attend la fin de mesure 
      gTarget = 0x81;
      gSMBNumBytesToRD = 4;
      SMB_Read();  // Initiate SMBus read
		//Delay_1ms(20);//attend la fin de mesure 
		
   return convertToTemp_i2c(((unsigned int )gSMBDataIN[1]<<8)+gSMBDataIN[2]);
}

/*---------------------------------------------------------------------------*-
   GetHumidite ()
  -----------------------------------------------------------------------------
   Descriptif: demande l'humidite ambiante au capteur EEH210
   Entrée    : --
   Sortie    : --
-*---------------------------------------------------------------------------*/
unsigned int GetHumidite()
{
   gTarget = 0x80;//0x81    (0x40 7 bit + 1 bit = 0x81 1 == read 
         gSMBDataOUT[0]  = 0xF5;
         gSMBNumBytesToWR = 1;
         SMB_Write();  // Initiate SMBus write
			while(SMB_BUSY);
		Delay_1ms(20);//attend la fin de mesure 
      gTarget = 0x81;
      gSMBNumBytesToRD = 4;
      SMB_Read();  // Initiate SMBus read
   return convertToHumi(((unsigned int )gSMBDataIN[1]<<8)+gSMBDataIN[2]);
}


/*---------------------------------------------------------------------------*-
configEeh210()
-----------------------------------------------------------------------------
Descriptif: Configure le capteur EEH210 
			fonction incomplete, il faut lire les parametre avant d'�crire
			dessus
Entree    : unsigned char tab[] - la chaine de caractere a decoder
Sortie    : --
-*---------------------------------------------------------------------------*/
void configEeh210(unsigned char mode)
{
	while(SMB_BUSY);
	gTarget = 0x80;//0x81    (0x40 7 bit + 1 bit = 0x81 1 == read 
  gSMBDataOUT[0]  = 0xE6;
	switch(mode)
	{
		case 0 :
			gSMBDataOUT[1]  = 0x3A;
		break;
		case 1 :
			gSMBDataOUT[1]  = 0x3B;
		break;
		case 2 :
			gSMBDataOUT[1]  = 0xBA;
		break;
		case 3 :
			gSMBDataOUT[1]  = 0xBB;
		break;
	}
	
  gSMBNumBytesToWR = 2;
  SMB_Write();  // Initiate SMBus write
}

/*---------------------------------------------------------------------------*-
convertToTemp()
-----------------------------------------------------------------------------
Descriptif: Convertie une valeur sur 16 bit en temperature
Entree    : unsigned int value - la donne a convertir
Sortie    : long - la temperature convertie avec un facteur 100
-*---------------------------------------------------------------------------*/
long convertToTemp_i2c(unsigned int value)
{
	value = value &~ 0x03;
	return (((long)value*17572)>>16)-4685;
}

/*---------------------------------------------------------------------------*-
convertToHumi()
-----------------------------------------------------------------------------
Descriptif: Convertie une valeur sur 16 bit en humidit�
Entree    : unsigned int value - la donne a convertir
Sortie    : unsigned int - la temperature convertie
-*---------------------------------------------------------------------------*/
unsigned int convertToHumi(unsigned int value)
{
	value = value &~ 0x03;
	return (((unsigned long)value*125)>>16)-6;;
}

/*---------------------------------------------------------------------------*-
ADCInit()
-----------------------------------------------------------------------------
Descriptif:
Pin + : P1.1
Pin - : GND
Aligner a Droite
Conversion sur : AD0BUSY=1;
Clock SAR : 2000000
ref sur 
Entree    : --
Sortie    : --
-*---------------------------------------------------------------------------*/
void ADCInit()
{

   AMX0P=0x00;//Entree positive sur P2.0
   AMX0N=0x1f;//Entree negative sur GND
            // +++++----- ADC0 SAR Conversion Clock Period Bits.
            // |||||+---- AD0LJST ajustement a droite
            // ||||||++-- Reserver
            // ||||||||  
   ADC0CF=0xb8;// 10111000 - clk SAR de 2000000Hz aligner a droite
               // +--------  ADC0 Enable Bit
               // |+-------  ADC0 Track Mode Bit.
               // ||+------- AD0INT ADC0 Conversion Complete Interrupt Flag
               // |||+------ AD0BUSY
               // ||||+----- ADC0 Window Compare Interrupt Flag
               // |||||+++-- ADC0 Start of Conversion Mode Select
               // ||||||||  
   ADC0CN=0x80;// 10000000
               // +--------- Reference Buffer Gain Select.
               // |++------- Unused
               // |||+------ Regulator Reference Override
               // ||||+----- Voltage Reference Select.
               // |||||+---- Temperature Sensor Enable Bit
               // ||||||+--- Internal Analog Bias Generator Enable Bit.
               // |||||||+-- On-chip Reference Buffer Enable Bit.
               // ||||||||  
   REF0CN=0x08;// 00010000

   EIE1|=0x08;
}
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

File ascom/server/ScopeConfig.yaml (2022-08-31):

name: 'Astrophotography Assistant'
descriptions: 'Ascom Alpaca interface to control my technician diploma project'
manufacturer: 'Tanguy Dietrich'
manufacturer_version: "1"
location: "Earth"
UUID: '424242424242'
driverinfo: "Simple driver to interface my technician diploma project"
driverversion: "1"
interfaceversion: "1"
supportedactions: ['', '']
configuration:
    alignmentmode: 1
    altitude: 46.09098
    aperturearea: 3.14
    aperturediameter: 3.14
    athome: False
    atpark: False
    azimuth: 3.14
    canfindhome: False
    canpark: False
    canpulseguide: True
    cansetdeclinationrate: True
    cansetguiderates: True
    cansetpark: False
    cansetpierside: False
    cansetrightascensionrate: True
    cansettracking: True
    canslew: True
    canslewaltaz: False
    canslewaltazasync: False
    canslewasync: False
    cansync: True
    cansyncaltaz: False
    canunpark: False
    declination: 0.0
    declinationrate: 15.04
    doesrefraction: False
    equatorialsystem: 0
    focallength: 1000.0
    guideratedeclination: 0.5
    guideraterightascension: 0.5
    ispulseguiding: False
    rightascension: 13.0
    rightascensionrate: 0.42
    sideofpier: -1
    siderealtime: 0.42
    siteelevation: 661.4
    sitelatitude: 660.4
    sitelongitude: 42.5
    slewing: False
    slewsettletime: 42
    targetdeclination: 0.0
    targetrightascension: 0.0
    tracking: True
    trackingrate: 0
    trackingrates: [0,1,2]
    utcdate: "2016-11-14T07:03:08.1234567Z"
    axisrates: [100, 15]
    canmoveaxis: True
    destinationsideofpier: -1

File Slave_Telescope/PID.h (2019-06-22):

/*===========================================================================*=
	Slave_Telescope - PID - Tanguy Dietrich
  =============================================================================
   Descriptif: 

=*===========================================================================*/

#define DEMO_CONSIGNE -200//45°C
#define CORRECTION_TEMPERATURE 50 //temperature a ajouter au dessus du point de rose

#define LM35_0_POS 0
#define LM35_0_NEG 1

#define LM35_1_POS 2
#define LM35_1_NEG 3

#define LM35_2_POS 4
#define LM35_2_NEG 5

#define LM35_3_POS 6
#define LM35_3_NEG 7

#define POT_0 8
#define POT_1 9
#define POT_2 10
#define POT_3 11



//Define Temperature
#define REF_ADC 322

#define MODE_UART 3
#define MODE_PID 2
#define MODE_POT 6

#define NMESURE 10 //nombre de mesure a faire pour une moyenne
#define DELAI_MESURE 10//temps entre chaque mesure * 50[ms]

#define KP 30
#define KI 0
#define KD 15

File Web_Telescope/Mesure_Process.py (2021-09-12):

import datetime
import time
import RPi.GPIO as GPIO
import serial
import json
import csv
import struct
import socket, select
from math import *

serial = serial.Serial("/dev/ttyS0",57600,timeout=1)

M_PI =  3.1415926535897932385
MOVE_SPEED = 48
flagPosition=1
UNITE_DEPLACEMENT = 49843#correspond a 15.04"arc
DEPLACEMENT_SECONDS_DEC = UNITE_DEPLACEMENT * MOVE_SPEED
DEPLACEMENT_SECONDS_RA_POS = UNITE_DEPLACEMENT * (MOVE_SPEED+1)#le ciel continue de bouger en meme temps
DEPLACEMENT_SECONDS_RA_NEG = UNITE_DEPLACEMENT * (MOVE_SPEED-1)
#serial = serial.Serial("/dev/ttyS0",57600,timeout=2)#
# List of socket objects that are currently open
open_sockets = []

# AF_INET means IPv4.
# SOCK_STREAM means a TCP connection.
# SOCK_DGRAM would mean an UDP "connection".
listening_socket = socket.socket( socket.AF_INET, socket.SOCK_STREAM )
listening_socket.setsockopt(socket.SOL_SOCKET, socket.SO_REUSEADDR, 1)

# The parameter is (host, port).
# The host, when empty or when 0.0.0.0, means to accept connections for
# all IP addresses of current machine. Otherwise, the socket will bind
# itself only to one IP.
# The port must greater than 1023 if you plan running this script as a
# normal user. Ports below 1024 require root privileges.
listening_socket.bind( ("", 10001) )

# The parameter defines how many new connections can wait in queue.
# Note that this is NOT the number of open connections (which has no limit).
# Read listen(2) man page for more information.
listening_socket.listen(5)

current_position = []

def StopRA():
    serial.write("RA0#")

def StopDEC():
    serial.write("DEC0#")

def RunDEC(direction):
    if direction==1:
        serial.write("DEC+#")
    else:
        serial.write("DEC-#")

def RunRA(direction):
    if direction==1:
        serial.write("RA+#")
    else:
        serial.write("RA-#")


def printit(ra_int, dec_int):
    h = ra_int
    d = floor(0.5 + dec_int*(360*3600*1000/4294967296.0));
    dec_sign = ''
    if d >= 0:
        if d > 90*3600*1000:
            d =  180*3600*1000 - d;
            h += 0x80000000;
        dec_sign = '+';
    else:
        if d < -90*3600*1000:
            d = -180*3600*1000 - d;
            h += 0x80000000;
        d = -d;
        dec_sign = '-';
    
    
    h = floor(0.5+h*(24*3600*10000/4294967296.0));
    ra_ms = h % 10000; h /= 10000;
    ra_s = h % 60; h /= 60;
    ra_m = h % 60; h /= 60;
    
    h %= 24;
    dec_ms = d % 1000; d /= 1000;
    dec_s = d % 60; d /= 60;
    dec_m = d % 60; d /= 60;

    print ("ra =", h,"h", ra_m,"m",ra_s,".",ra_ms)
    print ("dec =",dec_sign, d,"d", dec_m,"m",dec_s,".",dec_ms)


def GetTemperature_0():#temperature Ambiante
    serial.write("GET_T0#")
    temperature = serial.readline()
    #print temperature
    if temperature=="":
        return "ERREUR"
    else:
        #temperature=temperature[:4]+"."+temperature[4:]
        temperature=temperature.replace('\r',"")
        return temperature

def GetTemperature_1():
    serial.write("GET_T1#")
    temperature = serial.readline()
    if temperature=="":
        return "ERREUR"
    else:
        #temperature=temperature[:4]+"."+temperature[4:]
        temperature=temperature.replace('\r',"")
        return temperature

def GetTemperature_2():
    serial.write("GET_T2#")
    temperature = serial.readline()
    if temperature=="":
        return "ERREUR"
    else:
        #temperature=temperature[:4]+"."+temperature[4:]
        temperature=temperature.replace('\r',"")
        return temperature

def GetTemperature_3():
    serial.write("GET_T3#")
    temperature = serial.readline()
    if temperature=="":
        return "ERREUR"
    else:
        #temperature=temperature[:4]+"."+temperature[4:]
        temperature=temperature.replace('\r',"")
        return temperature

def GetTemperature_4():
    serial.write("GET_T4#")
    temperature = serial.readline()
    if temperature=="":
        return "ERREUR"
    else:
        #temperature=temperature[:4]+"."+temperature[4:]
        temperature=temperature.replace('\r',"")
        return temperature

def GetTemperature_Rose():
    serial.write("GET_TR#")
    temperature = serial.readline()
    if temperature=="":
        return "ERREUR"
    else:
        #temperature=temperature[:4]+"."+temperature[4:]
        temperature=temperature.replace('\r',"")
        return temperature

def GetHumidity():
    serial.write("GET_H#")
    humidity = serial.readline()
    if humidity=="":
        return "ERREUR"
    else:
        humidity=humidity.replace('\r',"")
        return humidity
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

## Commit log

2019-11-01 Remove Old version
    [2019-05-21 09_01_57.csv, 2019-05-23 10_34_35.csv, Config.cfg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]
2020-05-18 Divers amelioration
    [Master_Telescope V3.obj, Vitesse_Moteur.xlsx]
2020-07-09 Ajout du suivi de la comete C/2020 F3 (Neowise)
    [Master_Telescope V3.obj, Master_Telescope.obj, Master_Telescope_V2.obj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]
2021-09-12 Ajout d'un python qui permet de faire des plate solve sur des .NEF, et divers modification
    [2019-05-21 09_01_57.csv, 2019-05-23 10_34_35.csv, BrightStar.csv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]
2021-09-12 ajout de script utile a l'utilisation du projet
2022-08-29 Implemented all common method to ASCOM device
2022-08-31 Added configfile, and som uart communication
2022-08-31 Bug correction : no more write with put request after async load of yaml
    [ScopeConfig.yaml, Telescope.py]
